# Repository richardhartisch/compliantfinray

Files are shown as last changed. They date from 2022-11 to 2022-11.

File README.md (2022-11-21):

# Compliant Finray-Effect Gripper for High-Speed Robotic Assembly of Electrical Components

## Content  
The following directories contain the CAD files of the compliant finray-effect grippers. 

### Finray_FEA_models

Here a variety of finalized finray fingers can be found with varying infill direction and density, as .ipt or .stp files. This was mainly used for an FEA to compare experimental data, an alternative, fast approach was used to design the compliant finray grippers, which is described in "Slicing Process of Finray Models". Completely modeling the gruippers in CAD is not seen as an efficient way. 

### Finray_designs

Finray_designs contains the final iterations of the grippers used in the presented video, provided either as .ipt, .stp or .stl for your preferred slicer software. Finray_9 is the final iteration used for the experiments, however, Finray_8 provides a basis for own designs of the notch. Different versions of Finray_8_notch were used to test an additional contact surface. 

### Magazine

Here, the magazine used to achieve a constant known pose of the plug to be gripped can be found, as .ipt, .stp or .stl. The fixture is used as a contact plane for the plug, the spring is used to slightly press the plug against the fixture. The design was chosen to achieve generalisability to hold various plugs. 

### Mount

Here, the mount to connect the fingers with the gripper module can be found, as .ipt, .stp or .stl. Please note, that these were designed to fit the gripper module "IEG 76-030" from Weiss Robotics. 

## Slicing Process of Finray Models

The slicing software used was Ultimaker Cura. Here the parameters for the gripper can be set. The infill type is set to lines in Cura, to achieve the desired rib-structure, the option to connect infill lines is turned off. To allow compliance of the skin of the finger, the wall line count has to be set to one, with a line width close to the nozzle diameter (0.4 mm in my case). The line width of the infill is also set to 0.4 mm. The top and bottom layers are removed to fully achieve compliance through the ribs. In the first tests, infill densities of 10%, 20% and 30% were used, with the direction of the infill lines varying in 10 degree steps from 0° to 40°.

For the lower connecting section of the finger different slicing settings have to be used where Cura's "support blocker" feature is applied.
The support blocker allows dividing the two sections of the finger to change selected slicing parameters. For example, other than for the section of the fingers with the ribs, top and bottom layers are needed here. With the option "Per Model Settings" the wall/top/bottom thickness, wall line count and top/bottom layers can be changed individually for the section within the support blocker. This allows the part to be manufactured with individual settings.

If you're interested in working with the fingers with an additional contact plane keep in mind to add an additionall "support blocker" feature to the notches.

### Example of Support Blocker Feature in Cura:

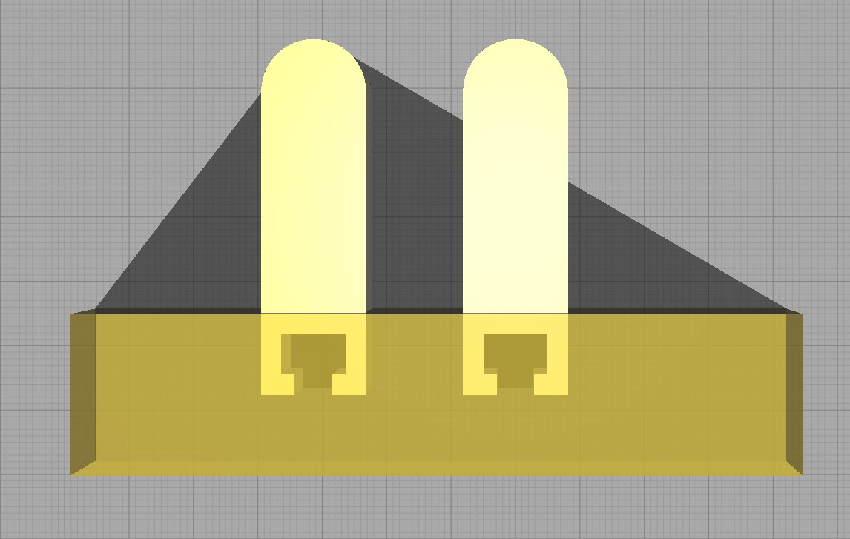
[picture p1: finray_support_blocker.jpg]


### Sliced Finray:

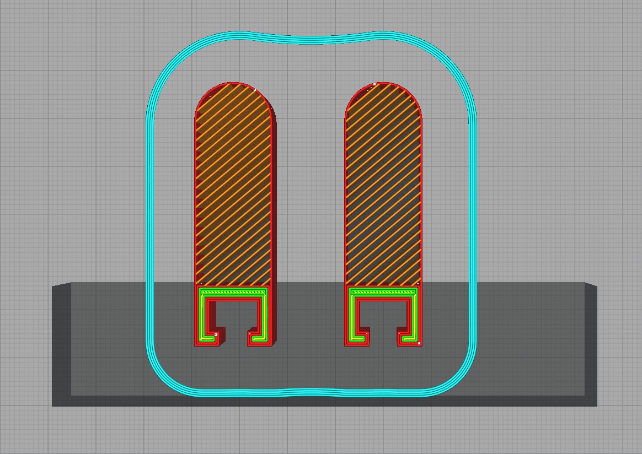
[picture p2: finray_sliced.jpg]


### Multiple Support Blockers for Additional Contact Surfaces:

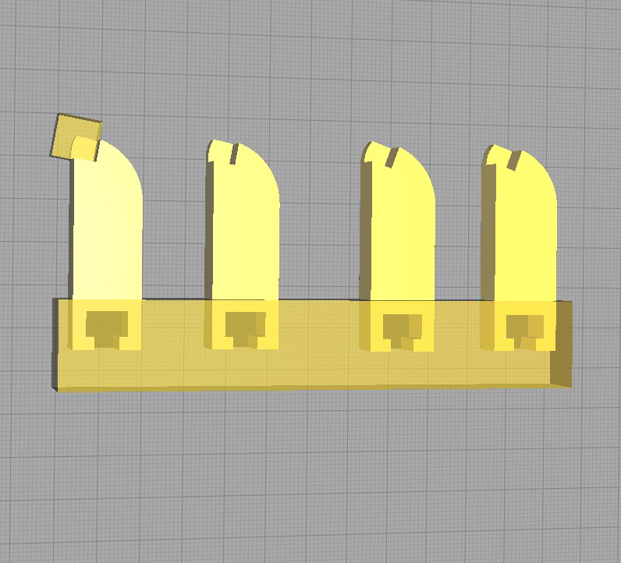
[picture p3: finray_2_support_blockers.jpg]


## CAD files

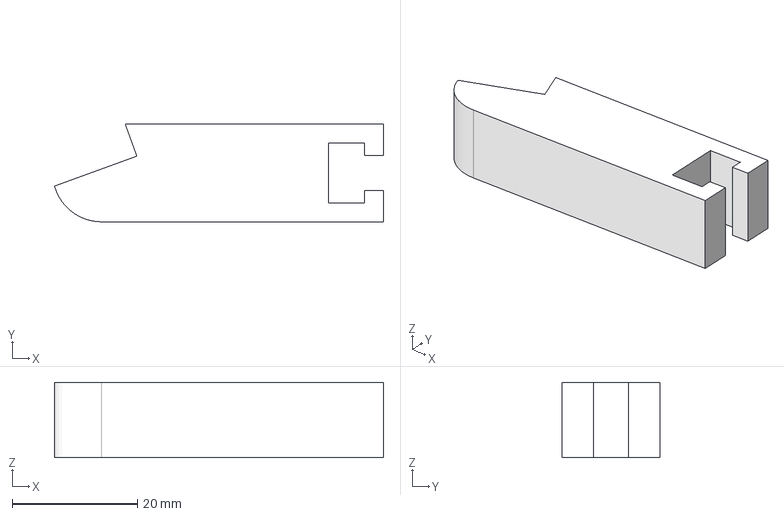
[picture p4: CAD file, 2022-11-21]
Finray_designs/Finray_8_notch_20deg.stp
52.5 x 15.6 x 12.0 mm

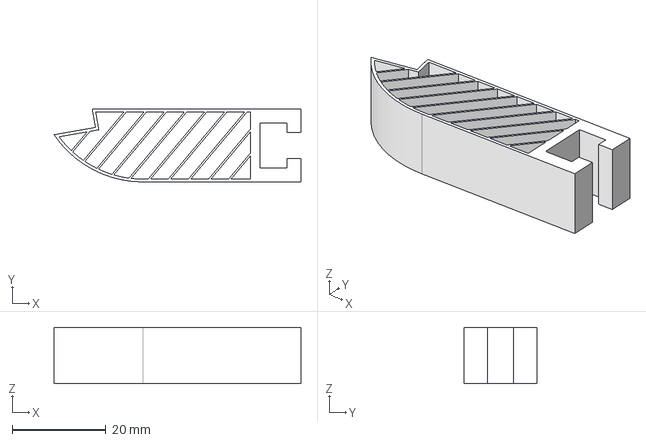
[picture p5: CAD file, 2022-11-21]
Finray_FEA_models/Finray_9_notch_10deg_40deg10inf.stp
52.8 x 15.6 x 12.0 mm

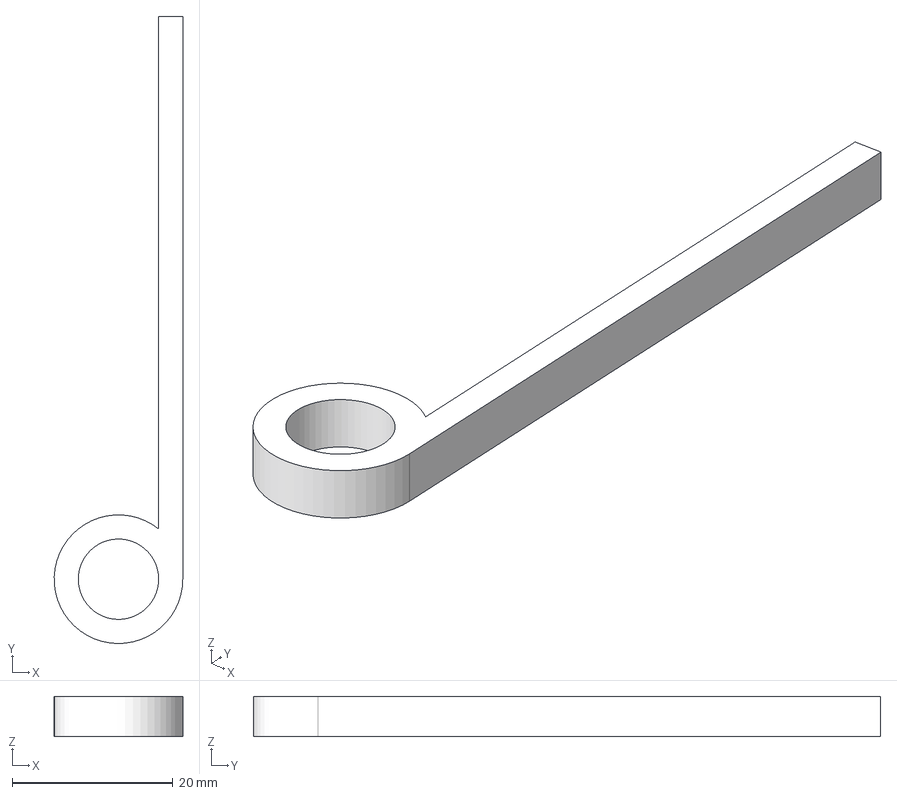
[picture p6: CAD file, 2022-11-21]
Magazine/spring.stp
16.0 x 78.0 x 5.00 mm

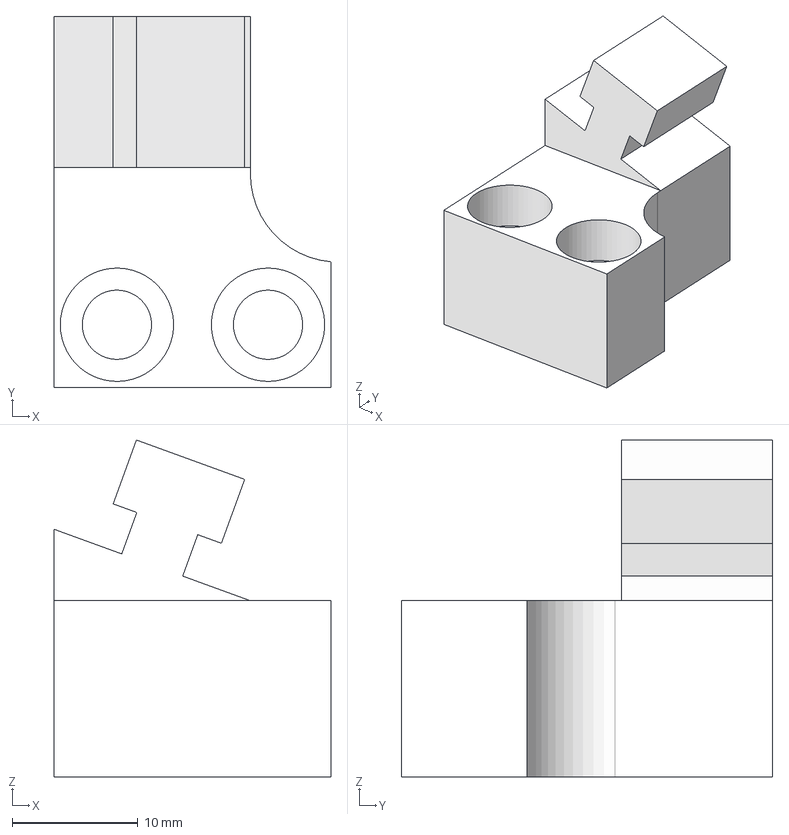
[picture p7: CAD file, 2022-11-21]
Mount/Mount_20deg.stp
22.0 x 29.5 x 26.8 mm

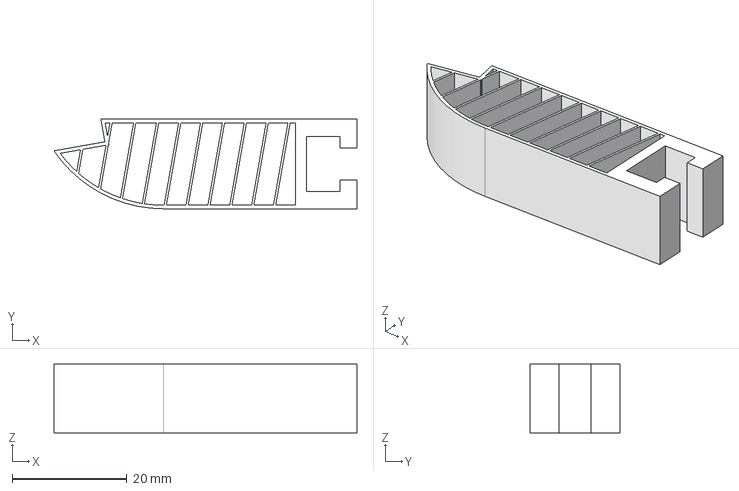
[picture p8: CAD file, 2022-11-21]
Finray_FEA_models/Finray_9_notch_10deg_10deg10inf.stp
52.8 x 15.6 x 12.0 mm

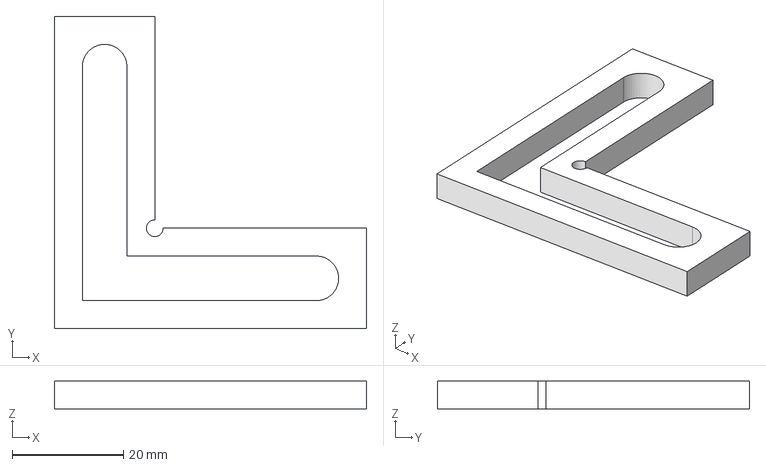
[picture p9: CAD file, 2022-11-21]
Magazine/fixture.stp
56.0 x 56.0 x 5.00 mm

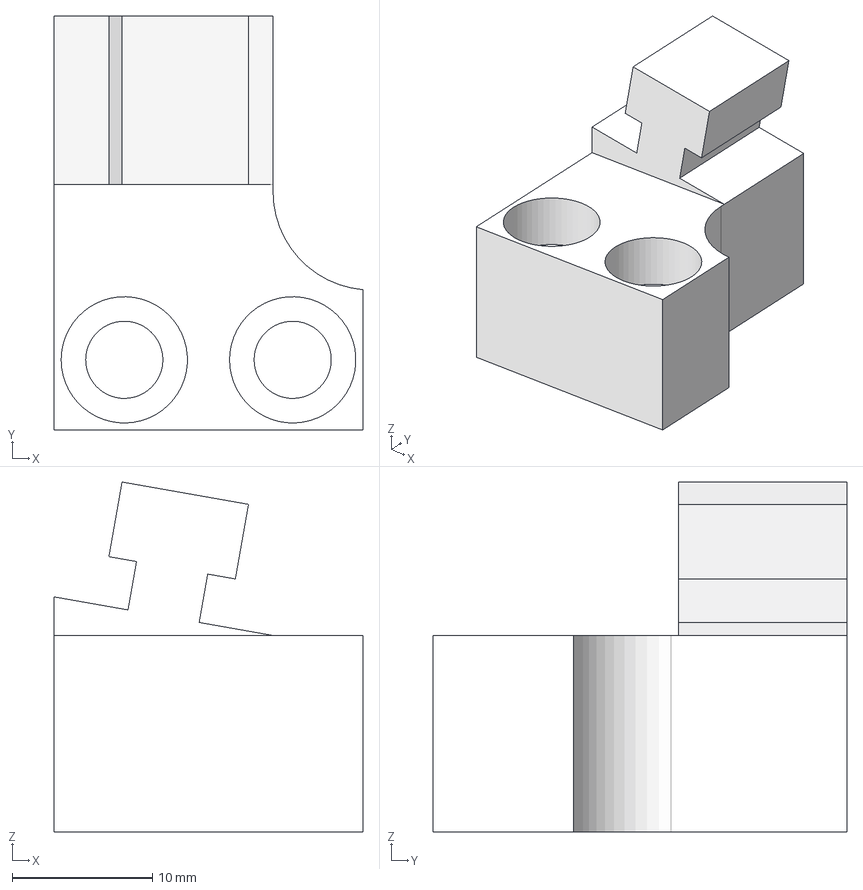
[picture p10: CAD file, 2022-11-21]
Mount/Mount_10deg.stp
22.0 x 29.5 x 24.9 mm

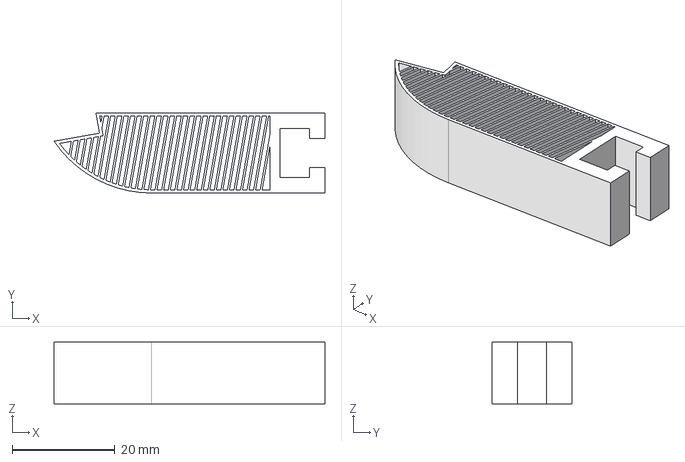
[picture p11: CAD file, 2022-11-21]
Finray_FEA_models/Finray_9_notch_10deg_10deg30inf.stp
52.8 x 15.6 x 12.0 mm

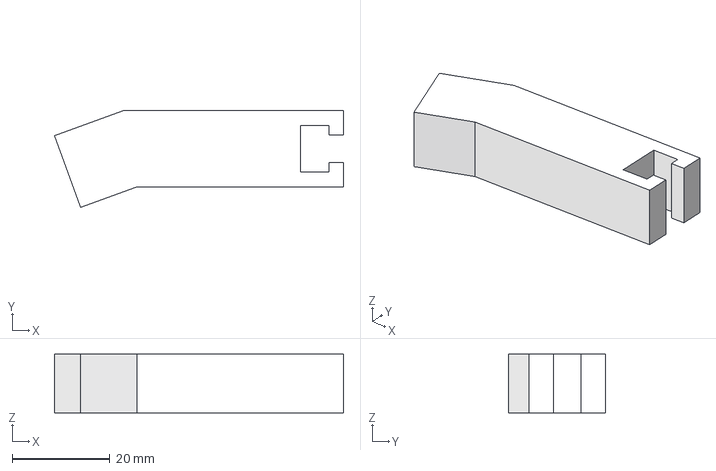
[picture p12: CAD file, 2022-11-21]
Finray_designs/Finray_8_flat_20deg.stp
59.1 x 19.8 x 12.0 mm

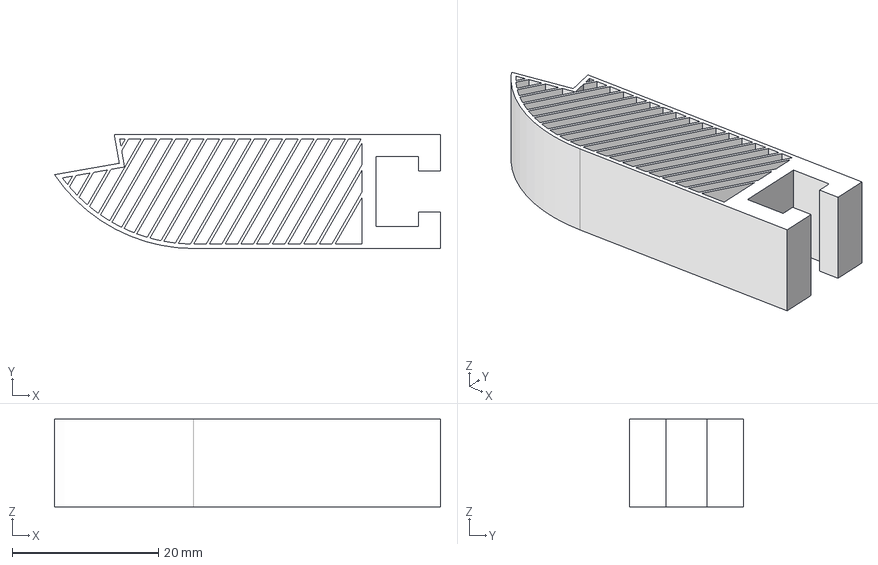
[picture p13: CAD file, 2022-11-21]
Finray_FEA_models/Finray_9_notch_10deg_30deg20inf.stp
52.8 x 15.6 x 12.0 mm

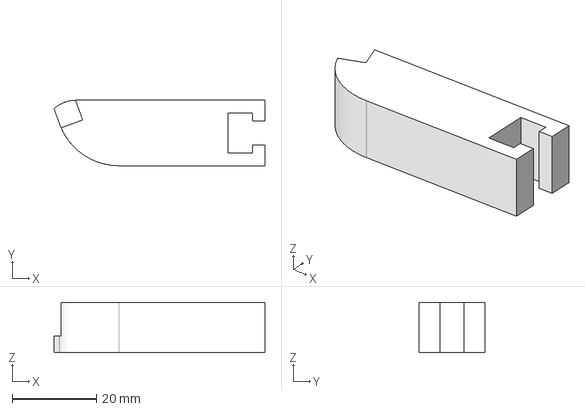
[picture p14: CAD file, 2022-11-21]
Finray_designs/Finray_8_notch_20deg_V4_right.stp
50.2 x 15.6 x 12.0 mm

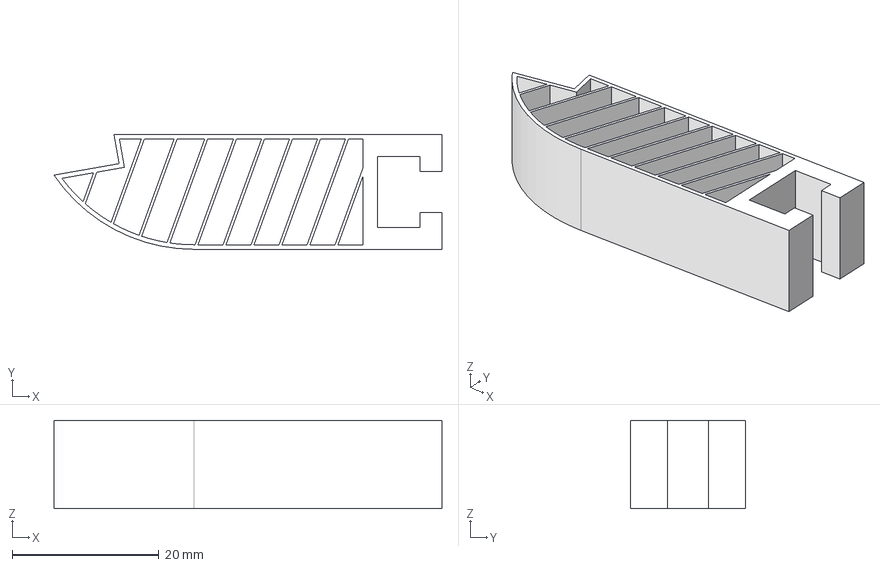
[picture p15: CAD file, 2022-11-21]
Finray_FEA_models/Finray_9_notch_10deg_20deg10inf.stp
52.8 x 15.6 x 12.0 mm

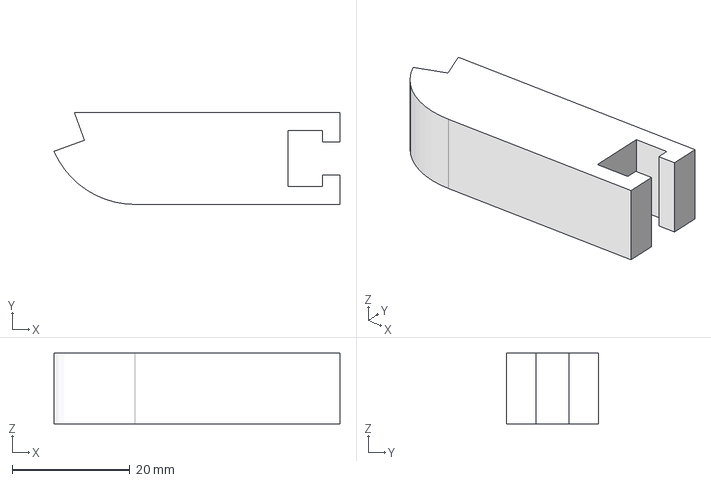
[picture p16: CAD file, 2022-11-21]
Finray_designs/Finray_8_notch_20deg_V3.stp
48.6 x 15.6 x 12.0 mm

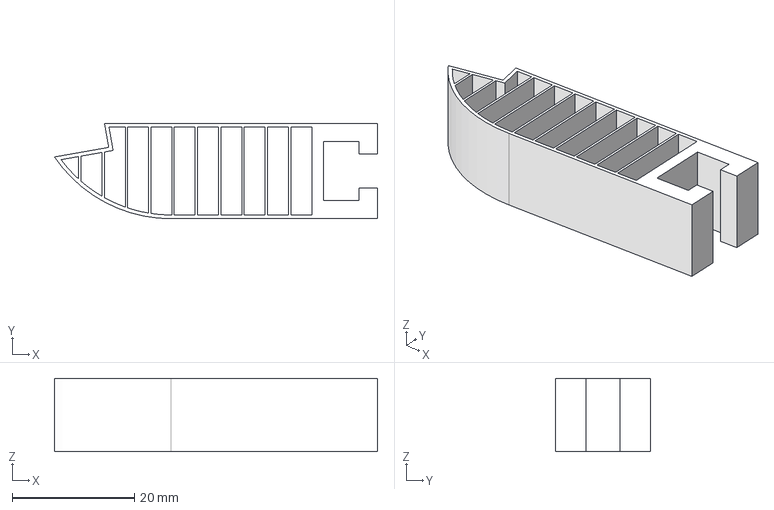
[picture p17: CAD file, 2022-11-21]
Finray_FEA_models/Finray_9_notch_10deg_0deg10inf.stp
52.8 x 15.6 x 12.0 mm

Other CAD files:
Finray_designs/Finray_9_notch_20deg.stp
Finray_designs/Finray_8_notch_20deg_V4_left.stp
Finray_FEA_models/Finray_9_notch_10deg_20deg30inf.stp
Finray_designs/Finray_8_notch_10deg_V3.stp
Finray_FEA_models/Finray_9_notch_10deg_0deg10inf.ipt
Finray_FEA_models/Finray_9_notch_10deg_0deg20inf.ipt
Finray_FEA_models/Finray_9_notch_10deg_0deg20inf.stp
Finray_FEA_models/Finray_9_notch_10deg_0deg30inf.ipt
Finray_FEA_models/Finray_9_notch_10deg_0deg30inf.stp
Finray_FEA_models/Finray_9_notch_10deg_10deg10inf.ipt
Finray_FEA_models/Finray_9_notch_10deg_10deg30inf.ipt
Finray_FEA_models/Finray_9_notch_10deg_20deg10inf.ipt
Finray_FEA_models/Finray_9_notch_10deg_20deg20inf.ipt
Finray_FEA_models/Finray_9_notch_10deg_20deg20inf.stp
Finray_FEA_models/Finray_9_notch_10deg_20deg30inf.ipt
Finray_FEA_models/Finray_9_notch_10deg_30deg10inf.ipt
Finray_FEA_models/Finray_9_notch_10deg_30deg10inf.stp
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
